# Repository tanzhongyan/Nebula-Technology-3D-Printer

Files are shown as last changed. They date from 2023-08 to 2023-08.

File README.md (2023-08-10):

# Nebula Technology COREXY 3D Printer (taobao)

## Description

This is an in-depth review regarding the most popular COREXY 3D Printer currently on [Taobao](https://item.taobao.com/item.htm?spm=a1z09.8149145.w4004-9653588878.3.400e6876iOqY7E&id=698708994651). It also contains useful marlin files and STLs required for this printer.
Coming in at 170USD before shipping, it has many upgrades and features compared to other COREXY printers out there for a fraction of the price. 

## Features

* Electronics
    * 360W 12V power supply
    * Motherboard
        * MKS GEN L V1.0
    * Stepper Drivers
        * TMC2209 (standalone) for X and Y Stepper Motors
        * A4988 for Z, Z2 and E0 Stepper Motors
        * Independent Dual Z control
    * ABL 
        * BL Touch Clone (3D Touch)
    * Titan Extruder Direct Drive Clone
    * MK8 Hotend
        * Generic 40W Heater Catridge
        * Generic 100k Thermistor
        * PID controlled
    * 300 x 300 Heated Bed
        * Bang-Bang controlled
    * MGN 12 Linear Rails for X and Y axis
    * Cooling Fans
        * 3010 Heatsink cooling Fan
        * 5015 Part Cooling Radial Fan

* Firmware
    * Ultimaker Cura 5.3.1
    * Marlin 2.1.2.1

## Comparison to Ender 5

Using Ender 5 as a comparison, there are a few noticeable upgrades. 
* Pros (Comared to Ender 5)
    * Linear Rails and Optical Shafts. Z rollers are notorious for causing binding and other issues
    * Direct Drive
    * Half the price. Ender 5 costing $550 USD

* Cons (Comared to Ender 5)
    * Lack support and community assistance. Most suitable for intermediate 3D Printing enthusiast
    * Takes approximately 40 hours of build time
    * You might be better off building other community sourced projects such as the Hypercube or Voron

## Issues

1. For non-mandarin speaking enthusiast, the project proves to be difficult as the tutorials, descriptions and after service are all in mandarin. 
2. The instructions lack some crucial information and requires some experience & research to solve.
3. There may be some missing parts. For us, we were lacking T8 lead screw nuts.
4. Insufficient tools provided.
5. The parts were all printed in PLA. STLs are also reserved for their private usage. We had to reverse engineer some of the provided parts.
6. Firmware provided did not work as intended. The language was in mandarin, encoder was reversed, direction of motors was reversed as well, X axis was now the Y axis and vice versa. We had to redo the marlin firmware to fix such issues.
7. Heated bed is not PID controlled, and takes 5 minutes to heat up.
8. The original power point was a 3 pin plug directly connecting between the power supply and the outlet socket. This was dangerous as there was no protective fuse and there were exposed wires.
9. Xloader firmware provided did not work.
10. Click to resume prompt after G29 ABL.

## Solutions

1. We used Google Translate to converse with the seller.
2. ChatGPT amd BingAI was effective in providing certain advice regarding marlin firmware configuration and issues faced.
3. As we had some CAD, Marlin and Cura experience, solving these issues took approximately 10 hours of troubleshooting.
4. Recommend to get a mosfet for the hotbed.
5. We bought a power switch socket with fuse and printed out a mount for it.
6. Kapton tape was essential in securing drooping wires.

## Conclusion

With increasingly advance 3D printers, we must analyse and balance the cost to benefit that comes with cheaper DIY projects. Personally, we were looking to use this 3D printer with a [Fystec Enraged Rabbit Carrot Feeder](https://item.taobao.com/item.htm?spm=a21n57.1.0.0.70dd523cJbnjHU&id=681765751259&ns=1&abbucket=2#detail) to do multicoloured prints and prototyping. We spent an approximate of $370USD for the 3D Printer and Fystec ERCF. We spent 50 hours assembling just the 3D Printer alone. If you took into account cost to benefit, purchasing a [BambuLab P1S Combo](https://detail.tmall.com/item.htm?spm=a21n57.1.0.0.14d7523cgGgQYl&id=695623155242&ns=1&abbucket=2) off taobao would make more sense. The P1S would also retain its value for years to come. However, we were able to learn many useful skills such as methodical thought processes, problem solving and critical thinking. More technical skills such as how a 3D printer functions and operate, and software related competencies.

### TL;DR

* Pros
    * Learn technical skills and competencies regarding 3D printers
    * Low cost and affordable
    * Potentially better than other prebuild options
* Cons
    * Time extensive
    * Cost to benefit not worth it

## Authors

[@TanZhongYan](https://www.linkedin.com/in/zhong-yan-tan/)
[@HoKheeXuan](https://www.linkedin.com/in/ho-khee-xuan-a8a35b1b0/)

## License

This project is licensed under the [Creative Commons Attribution-NonCommercial-NoDerivatives (CC BY-NC-ND) License](LICENSE.md).

## Acknowledgments

* [Nebula Technology 3D Printing](https://shop115693462.taobao.com/shop/view_shop.htm?shop_id=115693462&spm=a21m98.27004841)
* [Marlin Firmware](https://marlinfw.org/)
* [Xloader](https://github.com/binaryupdates/xLoader)

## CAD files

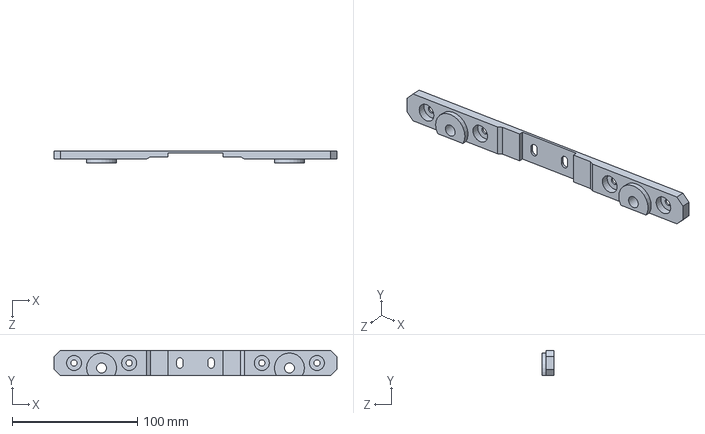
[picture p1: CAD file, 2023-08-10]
2. STL/Top Z Bracket.SLDPRT
226.0 x 20.0 x 9.60 mm

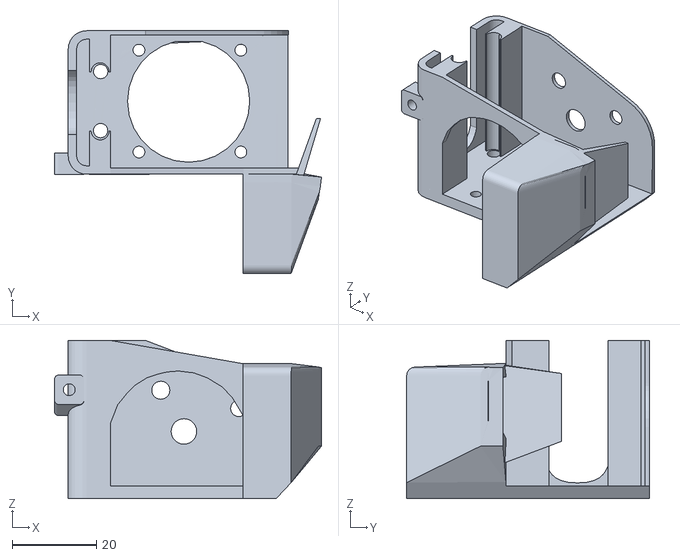
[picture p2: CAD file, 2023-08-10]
2. STL/6. Hotend Fan Shroud.stl
63.4 x 57.6 x 37.5

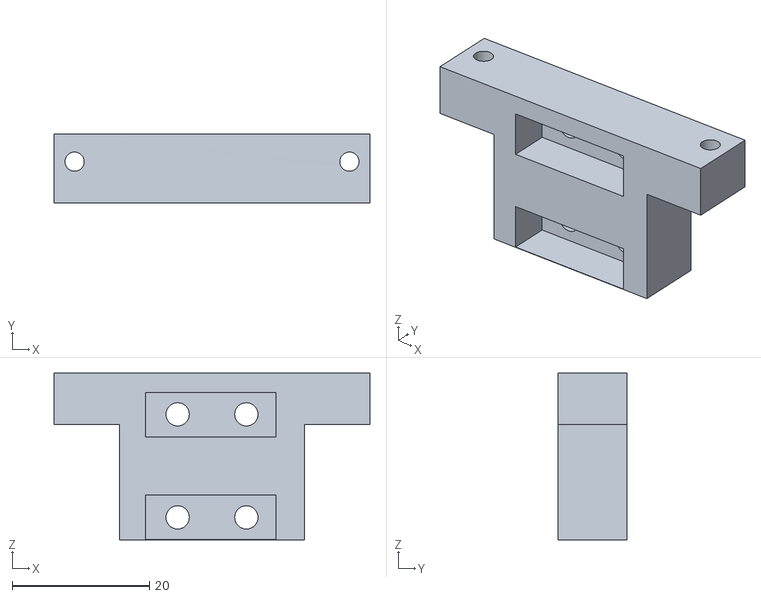
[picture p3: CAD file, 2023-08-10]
2. STL/7. XY Carriage Joiner.stl
46.0 x 10.0 x 24.3

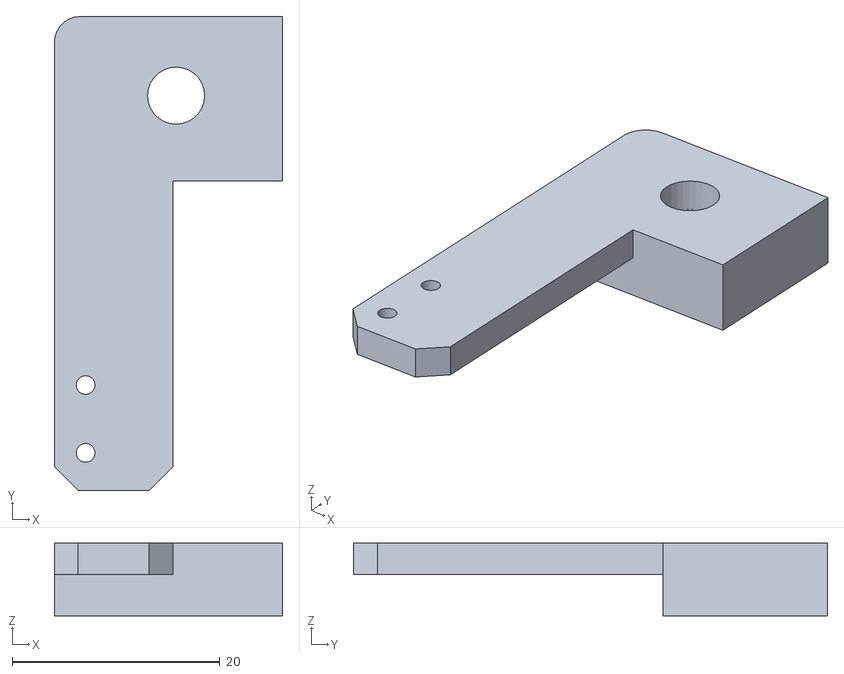
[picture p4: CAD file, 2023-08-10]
2. STL/4. Endstop Item.stl
22.0 x 45.7 x 7.00

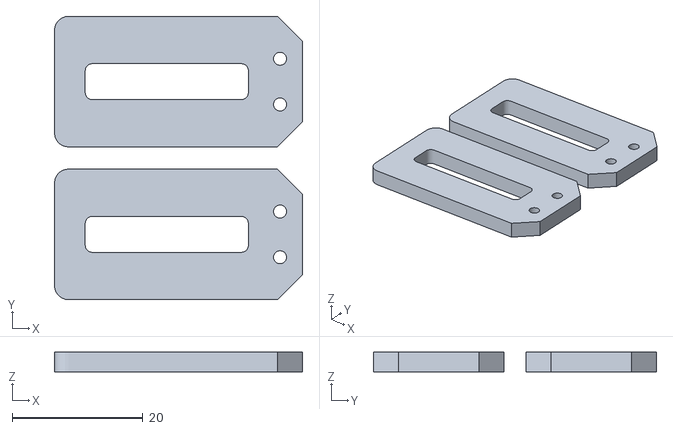
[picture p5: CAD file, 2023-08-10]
2. STL/5. Endstop Spacers.stl
38.0 x 43.4 x 3.00

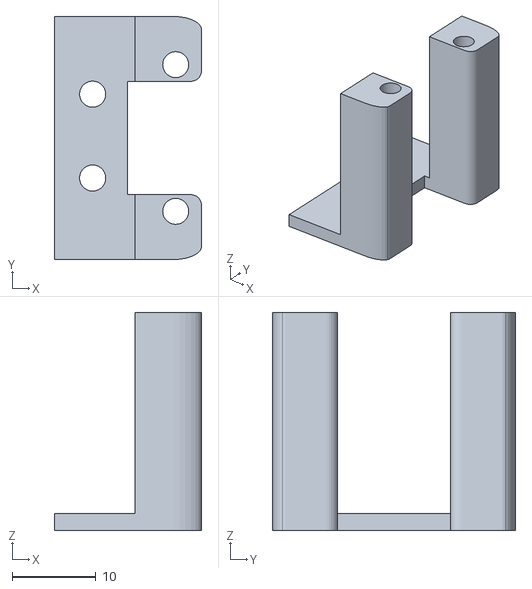
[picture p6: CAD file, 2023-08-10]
2. STL/3. ABL Mount.STL
17.6 x 29.0 x 26.0

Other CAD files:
2. STL/Bottom Z Bracket.SLDPRT
2. STL/1. Top Z Bracket.STL
2. STL/2. Bottom Z Bracket.STL

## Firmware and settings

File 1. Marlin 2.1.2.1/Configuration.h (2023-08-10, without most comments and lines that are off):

#pragma once
#define CONFIGURATION_H_VERSION 02010201
#define STRING_CONFIG_H_AUTHOR "(none, default config)" // Who made the changes.
#define SHOW_BOOTSCREEN
  #define MOTHERBOARD BOARD_MKS_GEN_L
#define SERIAL_PORT 0
#define BAUDRATE 250000
#define X_DRIVER_TYPE  TMC2209_STANDALONE
#define Y_DRIVER_TYPE  TMC2209_STANDALONE
#define Z_DRIVER_TYPE  A4988
#define Z2_DRIVER_TYPE A4988
#define E0_DRIVER_TYPE A4988
#define EXTRUDERS 1
#define DEFAULT_NOMINAL_FILAMENT_DIA 1.75
#define TEMP_SENSOR_0 1
#define TEMP_SENSOR_1 0
#define TEMP_SENSOR_2 0
#define TEMP_SENSOR_3 0
#define TEMP_SENSOR_4 0
#define TEMP_SENSOR_5 0
#define TEMP_SENSOR_6 0
#define TEMP_SENSOR_7 0
#define TEMP_SENSOR_BED 1
#define TEMP_SENSOR_PROBE 0
#define TEMP_SENSOR_CHAMBER 0
#define TEMP_SENSOR_COOLER 0
#define TEMP_SENSOR_BOARD 0
#define TEMP_SENSOR_REDUNDANT 0
#define DUMMY_THERMISTOR_998_VALUE  25
#define DUMMY_THERMISTOR_999_VALUE 100
#if TEMP_SENSOR_IS_MAX_TC(0)
  #define MAX31865_SENSOR_OHMS_0      100 // (Ω) Typically 100 or 1000 (PT100 or PT1000)
  #define MAX31865_CALIBRATION_OHMS_0 430 // (Ω) Typically 430 for Adafruit PT100; 4300 for Adafruit PT1000
#endif
#if TEMP_SENSOR_IS_MAX_TC(1)
  #define MAX31865_SENSOR_OHMS_1      100
  #define MAX31865_CALIBRATION_OHMS_1 430
#endif
#if TEMP_SENSOR_IS_MAX_TC(2)
  #define MAX31865_SENSOR_OHMS_2      100
  #define MAX31865_CALIBRATION_OHMS_2 430
#endif
#if HAS_E_TEMP_SENSOR
  #define TEMP_RESIDENCY_TIME         10  // (seconds) Time to wait for hotend to "settle" in M109
  #define TEMP_WINDOW                  1  // (°C) Temperature proximity for the "temperature reached" timer
  #define TEMP_HYSTERESIS              3  // (°C) Temperature proximity considered "close enough" to the target
#endif
#if TEMP_SENSOR_BED
  #define TEMP_BED_RESIDENCY_TIME     10  // (seconds) Time to wait for bed to "settle" in M190
  #define TEMP_BED_WINDOW              1  // (°C) Temperature proximity for the "temperature reached" timer
  #define TEMP_BED_HYSTERESIS          3  // (°C) Temperature proximity considered "close enough" to the target
#endif
#if TEMP_SENSOR_CHAMBER
  #define TEMP_CHAMBER_RESIDENCY_TIME 10  // (seconds) Time to wait for chamber to "settle" in M191
  #define TEMP_CHAMBER_WINDOW          1  // (°C) Temperature proximity for the "temperature reached" timer
  #define TEMP_CHAMBER_HYSTERESIS      3  // (°C) Temperature proximity considered "close enough" to the target
#endif
#if TEMP_SENSOR_REDUNDANT
  #define TEMP_SENSOR_REDUNDANT_SOURCE    E1  // The sensor that will provide the redundant reading.
  #define TEMP_SENSOR_REDUNDANT_TARGET    E0  // The sensor that we are providing a redundant reading for.
  #define TEMP_SENSOR_REDUNDANT_MAX_DIFF  10  // (°C) Temperature difference that will trigger a print abort.
#endif
#define HEATER_0_MINTEMP   5
#define HEATER_1_MINTEMP   5
#define HEATER_2_MINTEMP   5
#define HEATER_3_MINTEMP   5
#define HEATER_4_MINTEMP   5
#define HEATER_5_MINTEMP   5
#define HEATER_6_MINTEMP   5
#define HEATER_7_MINTEMP   5
#define BED_MINTEMP        5
#define CHAMBER_MINTEMP    5
#define HEATER_0_MAXTEMP 275
#define HEATER_1_MAXTEMP 275
#define HEATER_2_MAXTEMP 275
#define HEATER_3_MAXTEMP 275
#define HEATER_4_MAXTEMP 275
#define HEATER_5_MAXTEMP 275
#define HEATER_6_MAXTEMP 275
#define HEATER_7_MAXTEMP 275
#define BED_MAXTEMP      150
#define CHAMBER_MAXTEMP  60
#define HOTEND_OVERSHOOT 15   // (°C) Forbid temperatures over MAXTEMP - OVERSHOOT
#define BED_OVERSHOOT    10   // (°C) Forbid temperatures over MAXTEMP - OVERSHOOT
#define COOLER_OVERSHOOT  2   // (°C) Forbid temperatures closer than OVERSHOOT
#define PIDTEMP          // See the PID Tuning Guide at https://reprap.org/wiki/PID_Tuning
#define BANG_MAX 255     // Limits current to nozzle while in bang-bang mode; 255=full current
#define PID_MAX BANG_MAX // Limits current to nozzle while PID is active (see PID_FUNCTIONAL_RANGE below); 255=full current
#define PID_K1 0.95      // Smoothing factor within any PID loop
    #define DEFAULT_Kp  37.39
    #define DEFAULT_Ki   3.62
    #define DEFAULT_Kd 96.48
#define MAX_BED_POWER 255 // limits duty cycle to bed; 255=full current
#define MAX_CHAMBER_POWER 255 // limits duty cycle to chamber heater; 255=full current
  #define PID_FUNCTIONAL_RANGE 10 // If the temperature difference between the target temperature and the actual temperature
#define PREVENT_COLD_EXTRUSION
#define EXTRUDE_MINTEMP 170
#define PREVENT_LENGTHY_EXTRUDE
#define EXTRUDE_MAXLENGTH 200
#define THERMAL_PROTECTION_HOTENDS // Enable thermal protection for all extruders
#define THERMAL_PROTECTION_BED     // Enable thermal protection for the heated bed
#define THERMAL_PROTECTION_CHAMBER // Enable thermal protection for the heated chamber
#define THERMAL_PROTECTION_COOLER  // Enable thermal protection for the laser cooling
#define COREYX
#define USE_XMIN_PLUG
#define USE_YMIN_PLUG
#define USE_ZMIN_PLUG
#define USE_YMAX_PLUG
#define USE_ZMAX_PLUG
#define ENDSTOPPULLUPS
#define X_MIN_ENDSTOP_INVERTING false // Set to true to invert the logic of the endstop.
#define Y_MIN_ENDSTOP_INVERTING false // Set to true to invert the logic of the endstop.
#define Z_MIN_ENDSTOP_INVERTING false // Set to true to invert the logic of the endstop.
#define I_MIN_ENDSTOP_INVERTING false // Set to true to invert the logic of the endstop.
#define J_MIN_ENDSTOP_INVERTING false // Set to true to invert the logic of the endstop.
#define K_MIN_ENDSTOP_INVERTING false // Set to true to invert the logic of the endstop.
#define U_MIN_ENDSTOP_INVERTING false // Set to true to invert the logic of the endstop.
#define V_MIN_ENDSTOP_INVERTING false // Set to true to invert the logic of the endstop.
#define W_MIN_ENDSTOP_INVERTING false // Set to true to invert the logic of the endstop.
#define X_MAX_ENDSTOP_INVERTING false // Set to true to invert the logic of the endstop.
#define Y_MAX_ENDSTOP_INVERTING false // Set to true to invert the logic of the endstop.
#define Z_MAX_ENDSTOP_INVERTING false // Set to true to invert the logic of the endstop.
#define I_MAX_ENDSTOP_INVERTING false // Set to true to invert the logic of the endstop.
#define J_MAX_ENDSTOP_INVERTING false // Set to true to invert the logic of the endstop.
#define K_MAX_ENDSTOP_INVERTING false // Set to true to invert the logic of the endstop.
#define U_MAX_ENDSTOP_INVERTING false // Set to true to invert the logic of the endstop.
#define V_MAX_ENDSTOP_INVERTING false // Set to true to invert the logic of the endstop.
#define W_MAX_ENDSTOP_INVERTING false // Set to true to invert the logic of the endstop.
#define Z_MIN_PROBE_ENDSTOP_INVERTING false // Set to true to invert the logic of the probe.
#define DEFAULT_AXIS_STEPS_PER_UNIT   { 80, 80, 400, 392.15686 }
#define DEFAULT_MAX_FEEDRATE          { 200, 200, 40, 200 }
#define DEFAULT_MAX_ACCELERATION      { 1500, 1500, 200, 10000 }
#define DEFAULT_ACCELERATION          2000    // X, Y, Z and E acceleration for printing moves
#define DEFAULT_RETRACT_ACCELERATION  1500    // E acceleration for retracts
#define DEFAULT_TRAVEL_ACCELERATION   1500    // X, Y, Z acceleration for travel (non printing) moves
#define DEFAULT_EJERK    5.0  // May be used by Linear Advance
  #define JUNCTION_DEVIATION_MM 0.013 // (mm) Distance from real junction edge
  #define JD_HANDLE_SMALL_SEGMENTS    // Use curvature estimation instead of just the junction angle
#define Z_MIN_PROBE_PIN 15 // Pin 32 is the RAMPS default
#define BLTOUCH
#define NOZZLE_TO_PROBE_OFFSET { 0, -40, -2.4 }
#define PROBING_MARGIN 10
#define XY_PROBE_FEEDRATE (133*60)
#define Z_PROBE_FEEDRATE_FAST (4*60)
#define Z_PROBE_FEEDRATE_SLOW (Z_PROBE_FEEDRATE_FAST / 2)
#define Z_CLEARANCE_DEPLOY_PROBE   10 // Z Clearance for Deploy/Stow
#define Z_CLEARANCE_BETWEEN_PROBES  5 // Z Clearance between probe points
#define Z_CLEARANCE_MULTI_PROBE     5 // Z Clearance between multiple probes
#define Z_AFTER_PROBING           5 // Z position after probing is done
#define Z_PROBE_LOW_POINT          -2 // Farthest distance below the trigger-point to go before stopping
#define Z_PROBE_OFFSET_RANGE_MIN -20
#define Z_PROBE_OFFSET_RANGE_MAX 20
#define X_ENABLE_ON 0
#define Y_ENABLE_ON 0
#define Z_ENABLE_ON 0
#define E_ENABLE_ON 0 // For all extruders
#define DISABLE_X false
#define DISABLE_Y false
#define DISABLE_Z false
#define DISABLE_E false             // Disable the extruder when not stepping
#define DISABLE_INACTIVE_EXTRUDER   // Keep only the active extruder enabled
#define INVERT_X_DIR true
#define INVERT_Y_DIR false
#define INVERT_Z_DIR true
#define INVERT_E0_DIR false
#define INVERT_E1_DIR false
#define INVERT_E2_DIR false
#define INVERT_E3_DIR false
#define INVERT_E4_DIR false
#define INVERT_E5_DIR false
#define INVERT_E6_DIR false
#define INVERT_E7_DIR false
#define Z_HOMING_HEIGHT  10      // (mm) Minimal Z height before homing (G28) for Z clearance above the bed, clamps, ...
#define Z_AFTER_HOMING  10      // (mm) Height to move to after homing Z
#define X_HOME_DIR -1
#define Y_HOME_DIR -1
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

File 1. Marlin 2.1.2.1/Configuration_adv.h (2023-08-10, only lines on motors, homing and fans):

#define E0_AUTO_FAN_PIN -1
#define E1_AUTO_FAN_PIN -1
#define E2_AUTO_FAN_PIN -1
#define E3_AUTO_FAN_PIN -1
#define E4_AUTO_FAN_PIN -1
#define E5_AUTO_FAN_PIN -1
#define E6_AUTO_FAN_PIN -1
#define E7_AUTO_FAN_PIN -1
#define CHAMBER_AUTO_FAN_PIN -1
#define COOLER_AUTO_FAN_PIN -1
#define HOMING_BUMP_MM      { 5, 5, 2 }       // (linear=mm, rotational=°) Backoff from endstops after first bump
#define HOMING_BUMP_DIVISOR { 2, 2, 4 }       // Re-Bump Speed Divisor (Divides the Homing Feedrate)
  #define HOME_AFTER_G34
#define MICROSTEP_MODES { 16, 16, 16, 16, 16, 16 } // [1,2,4,8,16]

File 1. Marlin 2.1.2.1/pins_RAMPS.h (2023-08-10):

/**
 * Marlin 3D Printer Firmware
 * Copyright (c) 2020 MarlinFirmware [https://github.com/MarlinFirmware/Marlin]
 *
 * Based on Sprinter and grbl.
 * Copyright (c) 2011 Camiel Gubbels / Erik van der Zalm
 *
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
 */
#pragma once

/**
 * Arduino Mega with RAMPS v1.4 (or v1.3) pin assignments
 * ATmega2560, ATmega1280
 *
 * Applies to the following boards:
 *
 *  RAMPS_14_EFB (Hotend, Fan, Bed)
 *  RAMPS_14_EEB (Hotend0, Hotend1, Bed)
 *  RAMPS_14_EFF (Hotend, Fan0, Fan1)
 *  RAMPS_14_EEF (Hotend0, Hotend1, Fan)
 *  RAMPS_14_SF  (Spindle, Controller Fan)
 *
 *  RAMPS_13_EFB (Hotend, Fan, Bed)
 *  RAMPS_13_EEB (Hotend0, Hotend1, Bed)
 *  RAMPS_13_EFF (Hotend, Fan0, Fan1)
 *  RAMPS_13_EEF (Hotend0, Hotend1, Fan)
 *  RAMPS_13_SF  (Spindle, Controller Fan)
 *
 *  Other pins_MYBOARD.h files may override these defaults
 *
 *  Differences between
 *  RAMPS_13 | RAMPS_14
 *         7 | 11
 */

#if ENABLED(AZSMZ_12864) && DISABLED(ALLOW_SAM3X8E)
  #error "No pins defined for RAMPS with AZSMZ_12864."
#endif

#include "env_validate.h"

// Custom flags and defines for the build
//#define BOARD_CUSTOM_BUILD_FLAGS -D__FOO__

#ifndef BOARD_INFO_NAME
  #define BOARD_INFO_NAME "RAMPS 1.4"
#endif

//
// Servos
//
#ifndef SERVO0_PIN
  #ifdef IS_RAMPS_13
    #define SERVO0_PIN                        11
  #else
    #define SERVO0_PIN                        11
  #endif
#endif
#ifndef SERVO1_PIN
  #define SERVO1_PIN                           6
#endif
#ifndef SERVO2_PIN
  #define SERVO2_PIN                           5
#endif
#ifndef SERVO3_PIN
  #define SERVO3_PIN                           4
#endif

//
// Foam Cutter requirements
//

#if ENABLED(FOAMCUTTER_XYUV)
  #ifndef MOSFET_C_PIN
    #define MOSFET_C_PIN                      -1
  #endif
  #if HAS_CUTTER && !defined(SPINDLE_LASER_ENA_PIN) && NUM_SERVOS < 2
    #define SPINDLE_LASER_PWM_PIN              8  // Hardware PWM
  #endif
  #ifndef Z_MIN_PIN
    #define Z_MIN_PIN                         -1
  #endif
  #ifndef Z_MAX_PIN
    #define Z_MAX_PIN                         -1
  #endif
  #ifndef I_STOP_PIN
    #define I_STOP_PIN                        18  // Z-
  #endif
  #ifndef J_STOP_PIN
    #define J_STOP_PIN                        19  // Z+
  #endif
#endif

//
// Limit Switches
//
#ifndef X_STOP_PIN
  #ifndef X_MIN_PIN
    #define X_MIN_PIN                          3  // X-
  #endif
  #ifndef X_MAX_PIN
    #define X_MAX_PIN                          2  // X+
  #endif
#endif
#ifndef Y_STOP_PIN
  #ifndef Y_MIN_PIN
    #define Y_MIN_PIN                         14  // Y-
  #endif
  #ifndef Y_MAX_PIN
    #define Y_MAX_PIN                         15  // Y+
  #endif
#endif
#ifndef Z_STOP_PIN
  #ifndef Z_MIN_PIN
    #define Z_MIN_PIN                         18  // Z-
  #endif
  #ifndef Z_MAX_PIN
    #define Z_MAX_PIN                         19  // Z+
  #endif
#endif

//
// Z Probe (when not Z_MIN_PIN)
//
#ifndef Z_MIN_PROBE_PIN
  #define Z_MIN_PROBE_PIN                     32
#endif

//
// Steppers
//
#define X_STEP_PIN                            54
#define X_DIR_PIN                             55
#define X_ENABLE_PIN                          38
#ifndef X_CS_PIN
  #define X_CS_PIN                            53
#endif

#define Y_STEP_PIN                            60
#define Y_DIR_PIN                             61
#define Y_ENABLE_PIN                          56
#ifndef Y_CS_PIN
  #define Y_CS_PIN                            49
#endif

#ifndef Z_STEP_PIN
  #define Z_STEP_PIN                          46
#endif
#ifndef Z_DIR_PIN
  #define Z_DIR_PIN                           48
#endif
#ifndef Z_ENABLE_PIN
  #define Z_ENABLE_PIN                        62
#endif
#ifndef Z_CS_PIN
  #define Z_CS_PIN                            40
#endif

#ifndef E0_STEP_PIN
  #define E0_STEP_PIN                         26
#endif
#ifndef E0_DIR_PIN
  #define E0_DIR_PIN                          28
#endif
#ifndef E0_ENABLE_PIN
  #define E0_ENABLE_PIN                       24
#endif
#ifndef E0_CS_PIN
  #define E0_CS_PIN                           42
#endif

#ifndef E1_STEP_PIN
  #define E1_STEP_PIN                         36
#endif
#ifndef E1_DIR_PIN
  #define E1_DIR_PIN                          34
#endif
#ifndef E1_ENABLE_PIN
  #define E1_ENABLE_PIN                       30
#endif
#ifndef E1_CS_PIN
  #define E1_CS_PIN                           44
#endif

//
// Temperature Sensors
//
#ifndef TEMP_0_PIN
  #define TEMP_0_PIN                          13  // Analog Input
#endif
#ifndef TEMP_1_PIN
  #define TEMP_1_PIN                          15  // Analog Input
#endif
#ifndef TEMP_BED_PIN
  #define TEMP_BED_PIN                        14  // Analog Input
#endif

//
// SPI for MAX Thermocouple
//
#ifndef TEMP_0_CS_PIN
  #define TEMP_0_CS_PIN                       66  // Don't use 53 if using Display/SD card (SDSS) or 49 (SD_DETECT_PIN)
#endif
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

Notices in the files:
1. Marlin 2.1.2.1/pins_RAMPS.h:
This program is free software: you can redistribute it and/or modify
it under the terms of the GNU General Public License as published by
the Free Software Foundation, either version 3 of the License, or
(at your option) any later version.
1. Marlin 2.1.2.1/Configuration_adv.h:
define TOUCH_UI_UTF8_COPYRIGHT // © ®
